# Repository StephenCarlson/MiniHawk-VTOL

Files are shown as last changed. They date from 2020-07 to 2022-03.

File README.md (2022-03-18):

<!-- MiniHawk-VTOL README.md - Enable Word wrap in your Text Viewer/Editor -->
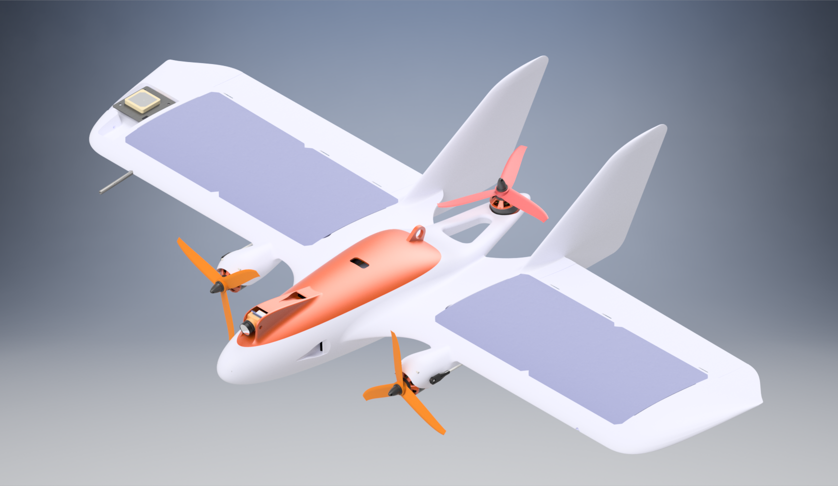
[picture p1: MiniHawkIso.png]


# MiniHawk-VTOL 
The MiniHawk VTOL is a 3D-Printed Tricopter/Fixed-wing hybrid aircraft, capable of Vertical Take-off and Landing. As with its predecessor, the [OrangeHawk VTOL](https://diydrones.com/profiles/blogs/the-orange-hawk-tricopter-flying-wing-vtol-uav), the MiniHawk is intended for R/C, FPV and UAV experimentation.  Mechanical artwork, build instructions, and configuration settings are provided in this repository.  

> **⚠️READ-ME - PROJECT STABILITY AND NEW VERSION⚠️ - 18 MARCH 2022: More than likely, you have stumbled on this project from a link on a YouTube video, such as [How NOT to Flight Test a VTOL UAV](https://www.youtube.com/watch?v=FYqH4kHllrU) or one of the other videos out there. If you want to try making this project, go for it! As of this writing, all the STL files on this repo, the _Version 2.0 - Hotfix and 2.1 Preview_ zip file at the left of this text, and the most recent upload to the Hackaday.io page are "safe". Previously, the were some design flaws (the old tilt nacelle design), but these issues only exist for Version 2.0 STLs from prior to the 23 February Hotfix. Again, everything present on the _master_ branch here should be safe to build and will not be altered for most of 2022.**
> 
> **Now, with that said, there is a new version coming out soon™, Version 2.1. However, at this point, this next version will not change any of the current STLs, so, again, you are totally safe to use the STLs, everything is working and flying great, and no changes to the aircraft design will be released until late this year or early next year. What the release of V2.1 will do is add some new bonus STLs/features, and otherwise it is just polishing presentation or rewriting documentation. I've been stuck in the prerelease of Version 2.1 for a few months, so some parts of this README are being rewritten, such as the build instructions and adding the Parts Tree Diagram and such. Here are my recommendations for building the project at this moment in time:**
> 
> - Refer to the [Development-Branch Build Instructions](https://github.com/StephenCarlson/MiniHawk-VTOL/tree/development#build-sequence-) for the updated build instructions.
> - Browse the [Development-Branch Documentation Folder](https://github.com/StephenCarlson/MiniHawk-VTOL/tree/development/doc-Documentation) for all the new build instruction images; many of these are not yet added or used in the updated build instructions.
> - Watch [MiniHawk-VTOL Assembly in 100 Seconds](https://www.youtube.com/watch?v=nICNlJhoEvw) to see the animated build steps.
> - Cross-reference with the [Older Build Instructions Below](https://github.com/StephenCarlson/MiniHawk-VTOL#build-sequence-). You will see images and steps for the older Version 1.0 release, so ignore features that do not exist or have been redesigned in the intervening 1.5 years.
> 
> **Sorry for the mess, I hope this helps. I enjoy promoting and polishing this project where I have time. Let me know if you have any questions, and have fun building! -Steve**

**Milestones**
| Date | Event |
|---|---|
| 15 Oct 2020  | Initial Release (v1.0) |
| 2 Oct 2021 | Version 2 (v2.0, MH7_ prefix) |
| prerelease | Version 2.1 |
| Q1 2023 | Version 2.2 |

Project Page at Hackaday: [HACKADAY.IO Page](https://hackaday.io/project/175286-minihawk-vtol)  

MiniHawk Design Details and Features discussed here: [RCGroups VTOLs Forum Thread](https://www.rcgroups.com/forums/showthread.php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)  

Featured MiniHawk-VTOL Builds by community members: [RCGroups 3D-Printed Forum Thread](https://www.rcgroups.com/forums/showthread.php?3750791-KatanaGuy-s-MiniHawk-VTOL)

Accompanying Build Video Series: [YouTube Playlist](https://www.youtube.com/playlist?list=PLEMjH2uELUcYI_DS1zthgjE4Su79LeA_G)  

Betaflight VTOL Firmware Build: [vtol-motor-mix](https://github.com/StephenCarlson/betaflight/tree/vtol-motor-mix)  

# Table of Contents
1. [Introduction](#head-brief)  
  1.1 [Description](#head-description)  
  1.2 [How To Use This Repo](#head-usage)  
  1.3 [Remarks / FAQs](#head-faqs)  
  1.4 [Metrics](#head-metrics)  
2. [Build Information](#build-brief)  
  2.1 [Recommended Tools](#build-tools)  
  2.2 [Components and Electronics](#build-components)  
  2.3 [Airframe Parts Listing](#build-airframeparts)  
3. [Build Steps](#buildseq-brief)  
  3.1 [Part 1 - Airframe Structures](#buildseq-part1)  
  3.2 [Part 2 - Linkages and Servos](#buildseq-part2)  
  3.3 [Part 3 - Electronics and Finishing](#buildseq-part3)  
4. [Flight Testing](#flight-brief)  
5. [3D Printing Guidelines](#3dprinting-brief)  
6. [ArduPlane](#arduplane-brief)  
  6.1 [R/C Controls Configuration](#arduplane-controlsconfig)  
  6.2 [Flight Controller Connections](#arduplane-connections)  
  6.3 [Parameters](#arduplane-parameters)  
  6.4 [Remarks](#arduplane-remarks)  
8. [License](#license-brief)  

## Description 
The MiniHawk is a 3D-Printed VTOL aircraft. It was designed with printability in mind, and is intended to provide the community with a common and accessible VTOL testbed for experimentation and tinkering. The vehicle uses three (3) brushless DC motors for propulsion, with the forward pair tilting for forward flight and yaw control, and the rear motor fixed for hover only. Four (4) servos are used to tilt the forward motors and to control the elevon control surfaces of the wing. The airframe is a "plank"-style wing with a center body containing avionics and battery, and internal conduits routing to the nacelles and servos. Twin vertical stabilizer fins provide mild directional stability.  

## How To Use This Repo 
This project is hosted on GitHub, which is traditionally a software repository site, but the format works well for a hardware project such as the MiniHawk-VTOL, where a few of the features come in handy:
- The history for each part file is accessible; if you need an old version, it is available even off-line if you've "cloned" the repo. (Beware, cloning the repo means hundreds of MB download.)
- [Versions and Releases](https://github.com/StephenCarlson/MiniHawk-VTOL/releases) are published just like a software project, and this includes setting milestones and planning future releases, keeping the community informed about what is next. Releases are the condensed set of essential files, placed in a zip archive, which represent a snapshot of the project at a moment when the artwork is stable and worth broad public distribution.
- The [Issues](https://github.com/StephenCarlson/MiniHawk-VTOL/issues) tab allow for the community to participate in the evolution of the design by providing feedback or contributions toward improving the design.
- The [Discussions](https://github.com/StephenCarlson/MiniHawk-VTOL/discussions) tab is another location for communication on the project.

While I have described the hosting environment, it isn't necessary for you to make a GitHub account or participate in the project; and more than likely, you are just interested in downloading the STLs and making the plane. Here is what you need to do:
- Click on the [Latest Release](https://github.com/StephenCarlson/MiniHawk-VTOL/releases/latest) in the Top-Right section of this webpage. This will take you to the most recent version of the design that was stable. 
- Read the description to understand what is new or notable for the release, and then look under the Assets section and find the .zip file named `MiniHawk-VTOL-x.x.x.zip`, where the 'x''s are the release version numbers. Skip the `Source Code` downloads as these are auto-generated by GitHub and represent the entire contents of the project, which you probably are not interested in unless you really want all of it.
- Unzip the archive and examine the files. A snapshot of this README you are reading is contained in the README.md file, and it should be able to be opened by any text editor.
- Follow the [Build Steps](#buildseq-brief) below. It should be possible to print this page or save as a PDF. If you are code-savvy, this is all written in Markdown and should render in whatever text editor or Markdown renderer you prefer.

## Remarks / FAQs 
- As this is a totally 3D-printed airframe, the fully-finished vehicle is moderately heavy, which is a handicap, especially in the hovering mode of flight. As such, be gentle and cautious in adding any additional weight. For the recommended print settings with a 0.4mm nozzle on standard PLA, the airframe alone weights a bit over 460g, and the all-up-weight of the finished vehicle is between 1000g to 1200g.  
- The parts used in this project are commonly available in the drone racing and R/C plane market(s). Standard motors such as 2207, 2306 or similar can be used. The nacelle design dictates a maximum motor bell diameter of 29mm, but this is relaxed compared to previous versions of the design that had more stringent requirements. The Ball-Stud Linkage is perhaps the most specific part used, with Dubro #181, Dubro #190, or even Dubro #367 as acceptable options. 
- The aerodynamics and stability of the vehicle are still under analysis and subject to revision. The CFD poses/cases used for aerodynamics analysis are included for independent study.  
- As of Version 2 of this design, project files are prefixed with "MH7", as this is the 7th internal revision of the design of the MiniHawk VTOL. There may be some old "MH5" parts are retained in the repo; these are from the old version(s). Also, the "MH#" prefix is incidental and not to be confused with the MH airfoil series, of which the MH45 is used for this vehicle. Generally, "MiniHawk-VTOL" is the correct name for this design and any revisions to be released.
- This vehicle was designed in Autodesk Inventor Professional 2019. While compiled STLs are provided as open-access, the Solid Model and Assembly Source files for this vehicle are withheld at the time of this writing; contact me for inquires on obtaining a copy or further development. One minor accommodation: STEP/STP versions of some parts such as the Hatch/Lid are included for community derivations.
- There are some variants to each part, such as versions of the nose with and without NACA vents. The Winglet is available as "normal" or with an excavation for a GPS or other devices. The Hatch/Lid has a FPV Variant, which supports the Foxeer -Nano camera formfactor (15mm width) and has a 30.5mm grid for a video transmitter, such as the AKK Infinite DVR. All the part options and variations are detailed below in the [Parts Tree Diagram](#build-airframeparts).

## Metrics 
| Description | Value |
|---|---|
| Wing Span | 800mm |
| Wing Area | 15.6dm^2 |
| Aspect Ratio | 4.1 |
| Airfoil (Root and Tip) | [MH45][1] |
| Length | 520mm |
| Rotor Spacing | 315mm Circle |
| Lipoly Battery | 4s, 1300-1500mAh (~160g)  |
| Motors (front) | 2207 or 2306 2300-2600kV  |
| Motor (rear) | 2207 or 2306 ~2000kV |
| Servos | HS-65HB/MG or eqv. |
| Flight Controller (size) | 30.50mm to 16.0mm Grid |
| Propellers (front) | 5050 to ~5249 |
| Propeller (rear) | 6030 to ~5249 |
| All-up Weight | 1000g to ~1200g w/ PLA |

[1]: <https://www.mh-aerotools.de/airfoils/mh45koo.htm> "MH45 Airfoil by Martin Hepperle"

# MiniHawk Build Parts List and Tools 
## Recommended Tools and Equipment 
 - FDM/FFF 3D Printer with build volume greater than 23.1x210.7x150mm (A build height of 330mm or greater will allow for printing the nose and wings as single parts rather than split.)
 - Soldering Station and associated tools and materials for electronics crafting
 - Handcrafting Tools: Pliers, Side-Cut Diagonal Cutters, Sandpaper, Hobby Knife/Scalpel, Hand Drill, etc
 - Adhesives and Consumables: Cyanoacrylate Glue, Hot-Melt Adhesive Gun, Tape

## Components and Electronics 
| Qty | Item Description | Notes |
|-----|---|---|
| 1 | Flight Controller (3 Motor, 4 Servo Outputs) | mRo PixRacer Pro, Matek F405-WING or F765-WING |
| - | Pitot Probe, GPS, Telem. Radios, FPV Cam+VTx, etc | Additional Essential Avionics |
| 1 | UBEC for servo power if not built into Flight Ctrlr. | Castle Creations 10 Amp Adjustable BEC |
| 1 | R/C Receiver, 8+ Channel, SBUS or PPM Output | |
| 3 | ESC (4s, 40A or better) | EMAX Formula Series 32Bit 45A ESC |
| 2 | 2207 or 2306 ~2500KV BLDC Motor (Out.Dia. < 29mm) | T-Motor VELOX V2 2207 2550Kv (Note 1) |
| 1 | 2207 or 2306 ~2000KV BLDC Motor | T-Motor VELOX V2 2306 1950Kv (Note 2) |
| 1 | 4s1300 Lipoly (60C or better) | RDQ 14.8V 4S 1300mAh 100C |
| 1 | XT60 Pigtail or equiv. | |
| 2 | HS-65HB Servo (or equiv.) | Elevon Servos, see (Note 3). |
| 2 | HS-5065MG Servo (or equiv.) | Motor Tilt Servos, see (Note 4). |
| 1 | Carbon Fiber Spar, Length<640mm, Out.Dia.<=6.5mm | Used to strengthen the wings. Round or Square |
| 6 | (opt) Du-Bro SKU#118 Small Nylon Hinge | Elevon Reinforcement, see (Note 5). |
| - | M2 or M3 Mounting Hardware (Nuts, Bolts, Standoffs)  | For mounting Flight Controller, trays. |
| 4 | 6-Inch Servo Extension Cable | (Note 6) |
| 1 | Male-to-Male Servo Extension Cable | Flight Controller to Receiver PPM/SBUS connection. |
| 4 | 2-56 Link Clevis (Note 7) | Four (4) servo arm connections. |
| 2 | 2-56 Threaded Linkage Rod, Length>=52mm | Elevon pushrods, L-bend at 45mm from threaded tip. |
| 2 | (opt) Du-Bro SKU#855 E/Z Links 0.72 (2-56) Clip | For securing L-Bends, can replace with Z-bend. |
| 2 | 1/16-inch 2-56 Ball Link and Coupler Pair | Dubro #181 or Dubro #190, see (Note 8). |
| 2 | 2-56 Fully-Threaded Rod, Length=70mm | End1=(Link 2-56 Clevis), End2=(2-56 Ball Coupler)  |
| 2 | 2-56 Smooth Rod, Length=40mm | (Note 9) |
| 4 | (opt) 3mm Bolt or Shaft, Length=44mm | If you want to use ball bearings to the tilt arms. |
| 4 | (opt) 3x6x2.5mm Ball Bearing | Commonly known as MR63ZZ, for tilt arm supports. |
| 2 | (opt) WS2812 5050 SMD (or equiv. Addressable LED) | Soldered with magnet wire, mounted in wingtips. |
| - | M4 or M5 Prop Nuts | Replace default prop nuts if needed |
| 1 | 50xx Propeller, Clockwise Rotation | Left/Port-side Propeller, 5-inch |
| 1 | 50xx Propeller, Counterclockwise Rotation | Right/Starboard-side Propeller, 5-inch |
| 1 | 50xx or 60xx Propeller, Counterclockwise Rotation | Tail Propeller, Dalprop Foldable F6 6048 Tri-blade |
| 1 | Velcro Battery Strap | |
| 1 | (opt) Battery Voltage Monitor / Alarm Buzzer | For Flight Controller if not included. |

> Note 1: Front motors should be no larger than OutsideDiameter=29mm, able to produce between 500g to 800g static thrust (@full-throttle), and pitch speed of ~20m/s (@half-throttle) with 5-inch prop.  
> Note 2: Tail motor may be up to OutsideDiameter=30mm or more, able to produce between 700g to 1000g static thrust (@full-throttle) with up to a 6-inch prop.  
> Note 3: Servo bays are designed for up to 26mm wide servos, 17.5mm from bottom of mounting tabs to bottom of servo, 32mm from top of output shaft to bottom of servo, 12mm thick. Should fit most "Sub-Micro" Servos.  
> Note 4: Same pocket dimensions as above, but these are going to be fantastically abused and must be fairly tough. Or just count on stripping your non-metal-gear servos a lot.  
> Note 5: Can be omitted, but 3D-printed living-hinge on elevons will eventually fail, mend appropriately. Dubro #118 is 6 per package, Dubro #119 for 15/pkg.  
> Note 6: Alternatively, cut the servo cables and solder in-line extensions for the cables to reach to the flight controller, plus some slack.  
> Note 7: The clevises and rods can be purchased as a set, such as Du-Bro #185, which is a set of 5 rods with clevises already attached.  
> Note 8: The Ball Link thread size should be 1/16-inch / 62.5mil / 1.59mm. A more popular variant of this type of part has a 2-56 (86mil) thread size ball, which a bit large but should be adaptable to the nacelle motor tilt mount part. If you can only order metric hardware, 2mm thread size should be fine. Note that this is the ball-link-stud thread size; the ball-link-stud attaches to the ball-link-socket/coupler that captures a threaded rod, which then links to the servo arm. This linkage rod which goes between the servo arm and the ball-link-socket/coupler can be any size, but is assumed to be 2-56 here.
> Note 9: Diameter=[1.83mm to 1.87mm], formed from spare pieces of 2-56 Servo Pushrod. Use non-threaded smooth rod, roughen/knurl only one end slightly for press-fitting to nacelle.  

## Airframe Parts 

```
MiniHawk-VTOL Version 2.1 Aircraft
|-- Fuselage/Body  
|   |-- Empennage/Tail
|   |   |-- Print Option 1: As a Single Part - No Split, but layers are not aligned for max. strength
|   |   |   |-- MH7_Empennage-Full.stl
|   |   |
|   |   |-- Print Option 2: Split into Two Parts with print layers aligned for strength
|   |       |-- Print Option 2a: Explicit Print Supports
|   |       |   |-- MH7_Empennage-PrintSupports.stl
|   |       |
|   |       |-- Print Option 2b: No Explicit Print Supports, plain part
|   |           |-- MH7_Empennage.stl
|   |
|   |-- Nose
|   |   |-- Print Option 1: Full Nose - No Split
|   |   |   |-- MH7_Nose.stl
|   |   |
|   |   |-- Print Option 2: Nose in Two Pieces
|   |       |-- MH7_Nose_A.stl
|   |       |-- MH7_Nose_B.stl
|   |
|   |-- Avionics (Flight Controller) Tray
|   |   |-- Part Variant: Solid Tray, No Vibration Dampening
|   |   |   |-- MH7_AvionicsTray.stl
|   |   |
|   |   |-- Part Variant: Leaf-Spring Compliant-Mechanism Vibration-Dampening Version
|   |       |-- MH7_AvionicsTray2.stl
|   |
|   |-- Battery Tray
|       |-- MH7_BatteryTray.stl
|
|-- Hatch/Lid
|   |-- Part Variant: FPV 16mm-sized Camera and VTx Support
|   |   |-- Print Option 1: Long-axis Symmetric Half (TODO: Needs to be restored to -Full)
|   |   |   |-- MH7_Hatch-FPV-16mm.stl
|   |   |
|   |   |-- Print Option 2: Split into Two Parts for nicer print
|   |       |-- MH7_Hatch-FPV-16mm_a.stl
|   |       |-- MH7_Hatch-FPV-16mm_b.stl
|   |
|   |-- Part Variant: Vented with NACA Duct
|   |   |-- Print Option 1: Entire thing, split it yourself
|   |   |   |-- MH7_Hatch-Vented.stl
|   |   |
|   |   |-- Print Option 2: Split into Two Parts for nicer print
|   |       |-- MH7_Hatch-Vented_a.stl
|   |       |-- MH7_Hatch-Vented_b.stl
|   |
|   |-- Locking Latch Mechanism
|       |-- MH7_Hatch_LockingLatch.stl
|       |-- 1.85mm Steel Pin, Length=30mm
|
|-- Left Wing  
|   |-- Part Variant: Plain Wing
|   |   |-- Print Option 1: Entire wing
|   |   |   |-- MH7_WingLeft.stl
|   |   |
|   |   |-- Print Option 2: Split into Two Parts for smaller printers
|   |       |-- MH7_WingLeft_A.stl
|   |       |-- MH7_WingLeft_B.stl
|   |
|   |-- Part Variant: Solar Wing
|   |   |-- Print Option 1: Entire wing
|   |   |   |-- MH7_WingLeft-Solar.stl
|   |   |
|   |   |-- Print Option 2: Split into Two Parts for smaller printers
|   |       |-- MH7_WingLeft_A.stl
|   |       |-- MH7_WingLeft_B.stl
|   |
|   |-- Elevon Control Horn
|       |-- MH7_ControlHorn.stl
|
|-- Left Fin  
|   |-- MH7_FinLeft_Lower.stl  
|   |-- MH7_FinLeft_Upper.stl  
|
|-- Left Nacelle
|   |-- Part Variant: Ball Bearing Version
|   |   |-- MH7_Nacelle_A-Bearing.stl
|   |   |-- MH7_Nacelle_B-Bearing.stl
|   |
|   |-- Part Variant: Non-Ball Bearing Version
|   |   |-- MH7_Nacelle_A-NoBearing.stl
|   |   |-- MH7_Nacelle_B-NoBearing.stl
|   |
|   |-- Motor Tilt-Mount
|       |-- Part Variant: Ball Bearing Version
|       |   |-- MH7_TiltMount_A-Bearing.stl
|       |   |-- 3mm Shaft or Threaded Bolt, Length=44mm
|       |
|       |-- Part Variant: Non-Ball Bearing Version
|       |   |-- MH7_TiltMount_A-NoBearing.stl
|       |   |-- 1.85mm Steel Pin, Length=40mm
|       |
|       |-- MH7_TiltMount_B.stl
|       |-- BLDC Motor
|    
|-- Left Winglet
|   |-- Part Variant: Plain Winglet
|   |   |-- MH7_WingletLeft.stl
|   |
|   |-- Part Variant: GPS Pocket
|       |-- MH7_WingletLeft-GPS.stl
|
|-- Right {Wing, Fin, Nacelle, Motor Tilt-Mount, Winglet} 
|   |-- For each of the symmetric parts, to create the right-side version, simply mirror the part in your slicer software. 
        Be _very careful_ please! Be sure you understand how all the parts go together, particularly the Nacelle pieces: 
        The nacelle _A piece is always near the aircraft center body, with the _B piece on the outboard side, aligned with 
        the servos and away from the center body. You should print four unique Nacelle pieces, with no two alike: 
        Two non-mirrored pieces of _A and _B, and two mirrored pieces of _A and _B.

Supporting Devices and Parts
|-- Weight & Balance Jackpoint Stand
|   |-- Nacelle-Support Beam
|   |   |-- MH7_WeightBalanceStand_Beam.stl
|   |   |-- MH7_WeightBalanceStand_Support.stl
|   |   |-- Two 1.85mm Steel Pins, Length=50mm each
|   |
|   |-- Empennage-Support Jack
|       |-- MH7_WeightBalanceStand_Foot.stl
|       |-- MH7_WeightBalanceStand_Support.stl (After gluing, bend the legs with hot water to form a triangle stance)
|       |-- 1.85mm Steel Pin, Length=50mm
|
|-- STEP/STP Version of the Hatch/Lid for Community Mods
    |-- MH7_Hatch_RELEASED.stp
```

# Build Sequence 
The following instructions assume that a full set of airframe parts have been printed, as enumerated above. Refer to the [3D Printing Guidelines Section](#3dprinting-brief) for details on the typical slicer settings for each part. Also, 3MF production files are available in the [3mf-Implementations](/3mf-Implementations) repo folder, but whether the print settings properly transfer to your particular printer is a bit of a gamble.

[Figure-1]: </doc-Documentation/Figure-1.png> "Figure 1 - Hinge Pin Clearance" 
[Figure-2]: </doc-Documentation/Figure-2.png> "Figure 2 - Elevon Movement Cuts"
[Figure-3]: </doc-Documentation/Figure-3.png> "Figure 3 - Hatch/Lid Bonding"
[Figure-4]: </doc-Documentation/Figure-4.png> "Figure 4 - Empennage Halves Bonding"
[Figure-5]: </doc-Documentation/Figure-5.png> "Figure 5 - Elevon Control Horn Install"
[Figure-6]: </doc-Documentation/Figure-6.png> "Figure 6 - Empennage/Tail Attachment"
[Figure-7]: </doc-Documentation/Figure-7.png> "Figure 7 - Nacelle Halves Bonding"
[Figure-8]: </doc-Documentation/Figure-8.png> "Figure 8 - Wing Attachment"
[Figure-9]: </doc-Documentation/Figure-9.png> "Figure 9 - Nacelle Pocket Finishing"
[Figure-10]: </doc-Documentation/Figure-10.png> "Figure 10 - Shaft and Bolt Hole Reaming"
[Figure-11]: </doc-Documentation/Figure-11.png> "Figure 11 - Nacelle Attachment"
[Figure-12]: </doc-Documentation/Figure-12.png> "Figure 12 - Vertical Stabilizer Attachment"
[Figure-13]: </doc-Documentation/Figure-13.png> "Figure 13 - Strake Attachment"
[Figure-14]: </doc-Documentation/Figure-14.png> "Figure 14 - Linkages and Movements"
[Figure-15]: </doc-Documentation/Figure-15.png> "Figure 15 - Propeller Rotation Directions"
[Figure-16]: </doc-Documentation/Figure-16.png> "Figure 16 - Center of Mass"

## Part 1 - Airframe Structures and Motor Mount/Tilt Attachment 
1. Clean all 3D-Printed parts, remove all brim/support material. Remove any burrs or blemishes. For each wing, carefully carve away any stringing or over-extrusion in the hinge reinforcement wells such that the hinge pin will fit. [Figure-1] The pitot-probe shaft and other small features may also have stringing that should be removed.  

2. Carefully cut the elevons free if needed (**WARNING!** Only cut slots on either end to allow for surface deflection, DO NOT cut the entire elevon out). [Figure-2] Gently exercise each surface up and down until the living hinge is established. The best way to start is to bend the elevons downward (as if pitching nose down) with a solid planar object to distribute the pressure on the control surface evenly. Only go as far as you feel comfortable, and then reverse direction. Continue to exercise the hinge gently until it is moving +/- 30 degrees. If you printed with PLA or another work-hardening material, don't continue cycling the hinge until the reenforcement tape or tabs are installed; only then should the hinge be further broken-in until it has smooth movement.  

<!-- Hey, if you are reading this, GitHub makes it really hard to inject pictures in a table with nice rows and spacing. -->
<!-- The HTML below renders the figures nicely in GitHub as of December 2021, may not work in other Markdown Processors. -->
<table style="width:100%">
  <tr>
    <td><figure>
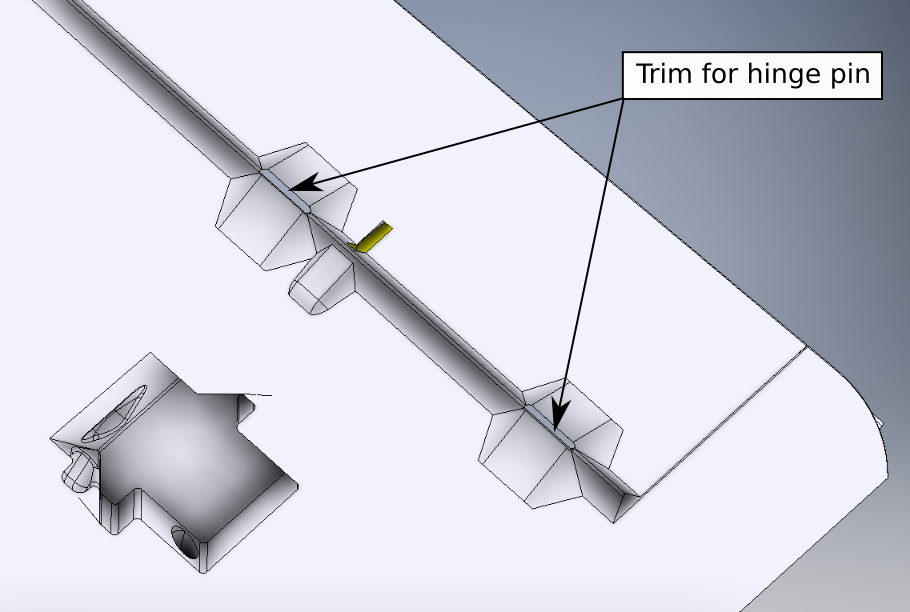
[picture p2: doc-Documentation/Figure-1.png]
      <br>
      <figcaption>Figure 1. Hinge Pin Clearance</figcaption></figure></td>
    <td><figure>
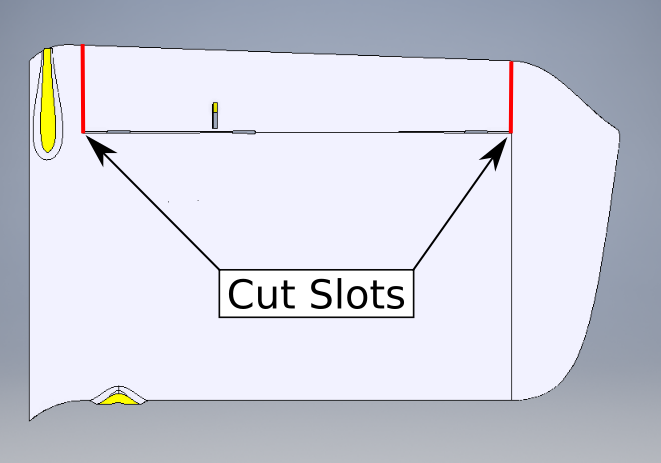
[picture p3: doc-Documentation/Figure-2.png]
      <br>
      <figcaption>Figure 2. Elevon Movement Cuts</figcaption></figure></td>
  </tr>
</table> 

3. Bond the Canopy/Hatch-Lid pieces together using Thin/Medium Cyanoacrylate and set aside to cure. [Figure-3]  

4. Bond the Empennage Halves together using Cyanoacrylate. (Skip this step if you printed the -Full one-piece version.) Set aside to cure. [Figure-4]  

<table style="width:100%">
  <tr>
    <td><figure>
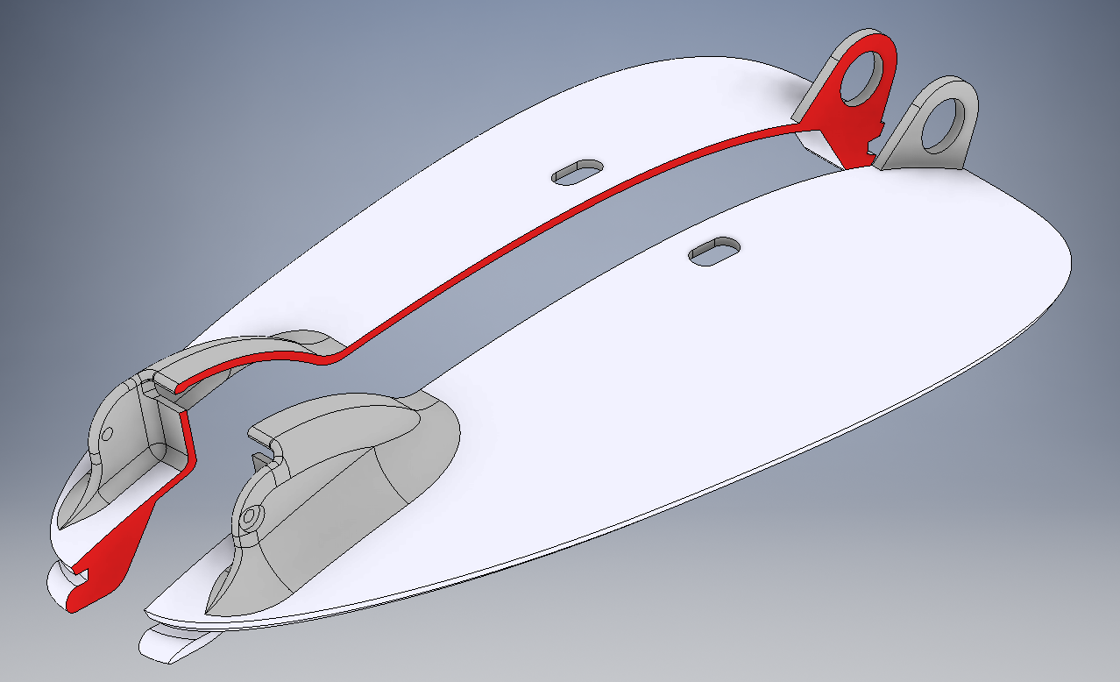
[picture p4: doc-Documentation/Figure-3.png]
      <br>
      <figcaption>Figure 3. Hatch/Lid Bonding</figcaption></figure></td>
    <td><figure>
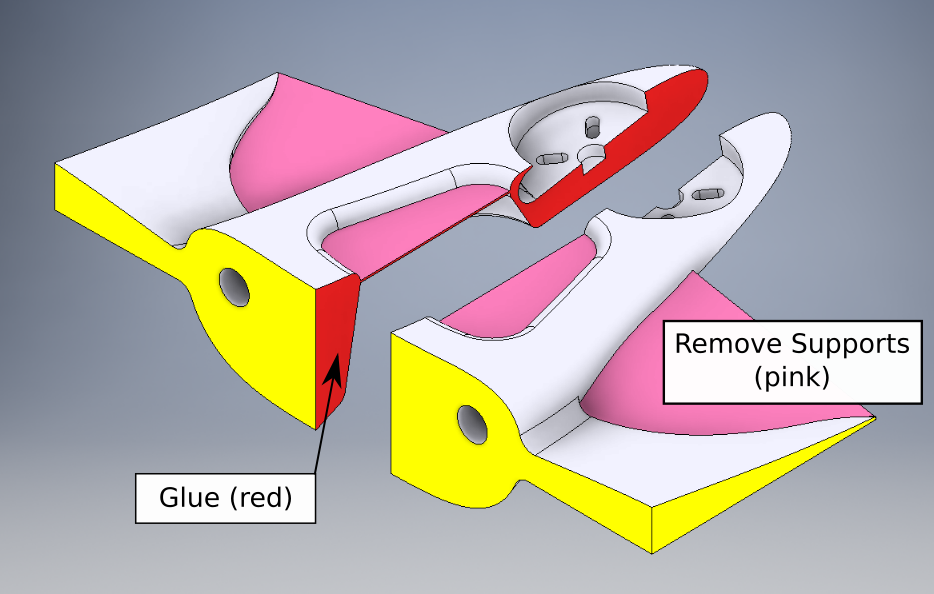
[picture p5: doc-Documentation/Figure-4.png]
      <br>
      <figcaption>Figure 4. Empennage Halves Bonding</figcaption></figure></td>
  </tr>
</table> 

5. Press-fit the Control Horn pieces into the elevons to test the fit. The Control Horn is inserted from the top, protruding through the elevon with the hole centered below the hingeline, inline with the elevon servo linkage. The pieces should be fairly flush on the Elevon Top Surface, with approximately 0.5mm extending above the surface. The fit should be tight, but do not force the control horn too hard or you may split print layers and cause damage. If it is too tight, carefully carve away any burrs or over-extrusion from the slot in the elevon, or sand the control horn to be thinner. Bond the Control Horn pieces (2) into each Elevon (Left Wing and Right Wing) using Cyanoacrylate. [Figure-5]  

6. Glue the Du-Bro Nylon Mini-Hinge pieces (3 per wing, Du-Bro SKU#118) into the recesses along each elevon hinge. Hot-Melt-Adhesive or Cyanoacrylate should work. 3M™ Transpore™ Surgical Tape is also a viable hinge reenforcement solution, and this may be applied now or later in the build.  

7. Lightly sand the bonded empennage/tail interface surface until smooth and planar/flush. Test-fit to the Fuselage/Nose to confirm a proper flush joint, and then bond to the Fuselage/Nose using Cyanoacrylate. Set aside to cure. [Figure-6]  

<table style="width:100%">
  <tr>
    <td><figure>
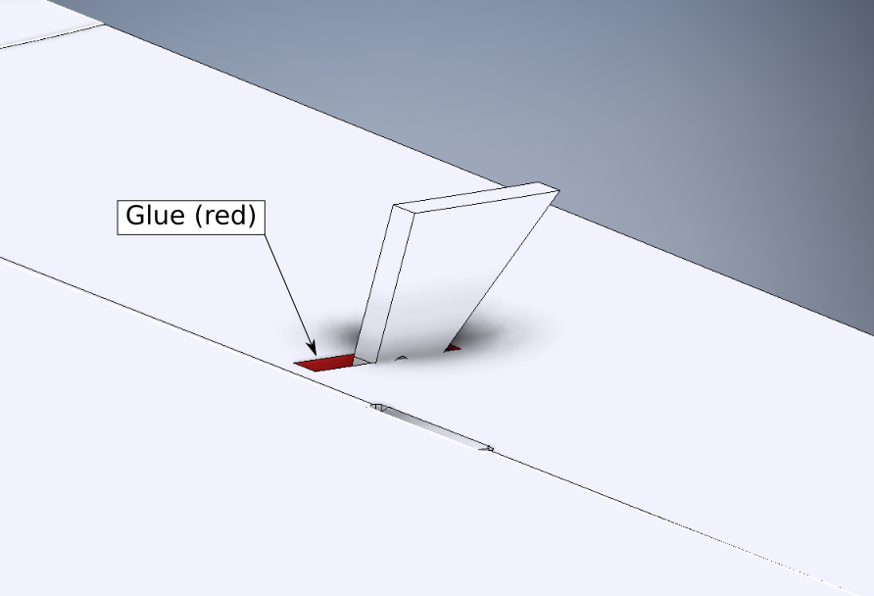
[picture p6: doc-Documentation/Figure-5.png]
      <br>
      <figcaption>Figure 5. Elevon Control Horn Install (Insert from top into slot)</figcaption></figure></td>
    <td><figure>
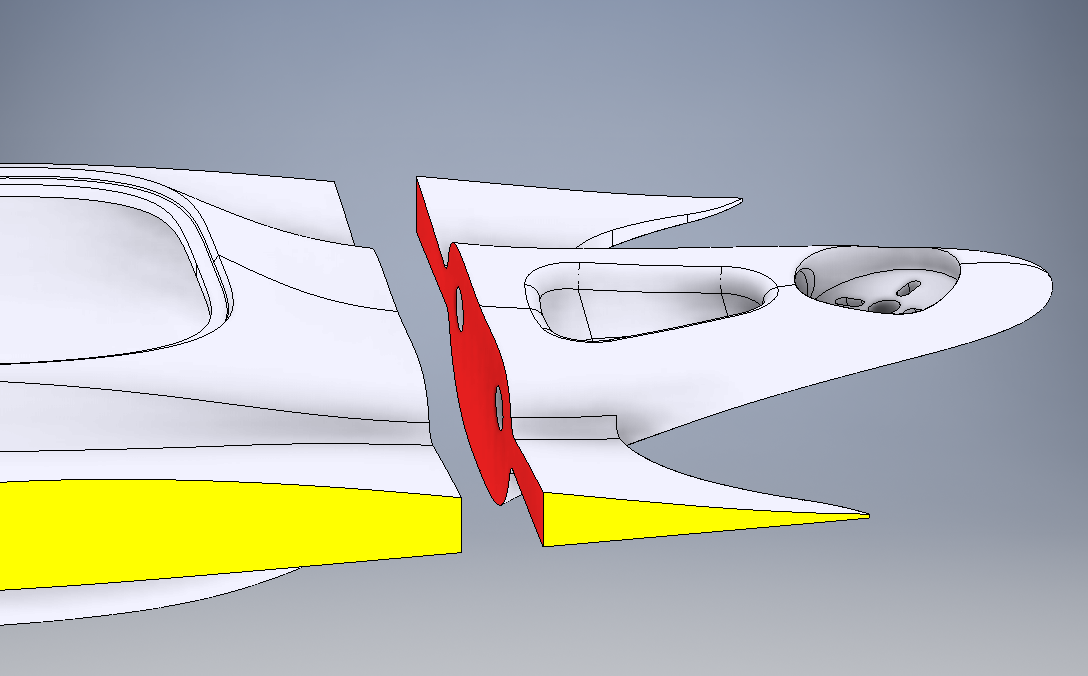
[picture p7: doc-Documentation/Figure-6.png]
      <br>
      <figcaption>Figure 6. Empennage/Tail Attachment</figcaption></figure></td>
  </tr>
</table> 

8. Bond the Nacelle Pair Halves together; **Be careful here!** Each nacelle is composed of an `_A` and `_B` piece. There should be four nacelle pieces total, and each of them is unique: An `_A` and `_B` that are non-mirrored, and a `_A` and `_B` that are mirrored. The `_A` has no cutout for the stud-arm, while the `_B` does. The `_A` pieces are always nearest the center body of the aircraft, and the `_B` pieces are always on the outside aligned with the servos. Glue the pieces together as carefully and precisely as possible, using Cyanoacrylate. Set aside to cure. [Figure-7]  

9. Lightly sand both wing root interface surfaces on the completed fuselage/body until flush and smooth. Test-fit the carbon-fiber spar and verify that it isn't being halted by any blemishes in the spar shaft in either wing. Get creative if there are blemishes; usually some aggressive poking with the spar will clear these without damaging the 3D-printed shaft. If the spar does not completely fill the spar shaft (7mm inside diameter), such as if the carbon spar is a 5mm round tube, then improvise a shim or other filler to make the fit snug, such as wrapping the spar with tape at the ends and near the center where it will exit into the central body cavity. With the spar present to provide alignment, test-fit both wings to each respective surface to confirm a proper flush joint. Center the spar such that it extends into the left and right wings an equal amount. (640mm is the longest spar length supported. A shorter spar is fine provided it is centered.) Remove the wings. At this point, the spar may be bonded to the body, if desired. (The spar can be installed without any adhesive if you plan on reusing it later, such as if the aircraft is totaled but the spar survives.) Bond either the left or right wing to the fuselage (not recommended to attach both at once) using Cyanoacrylate. Set aside to cure. When the first wing is cured, bond the second wing and set aside to cure. [Figure-8]  

<table style="width:100%">
  <tr>
    <td><figure>
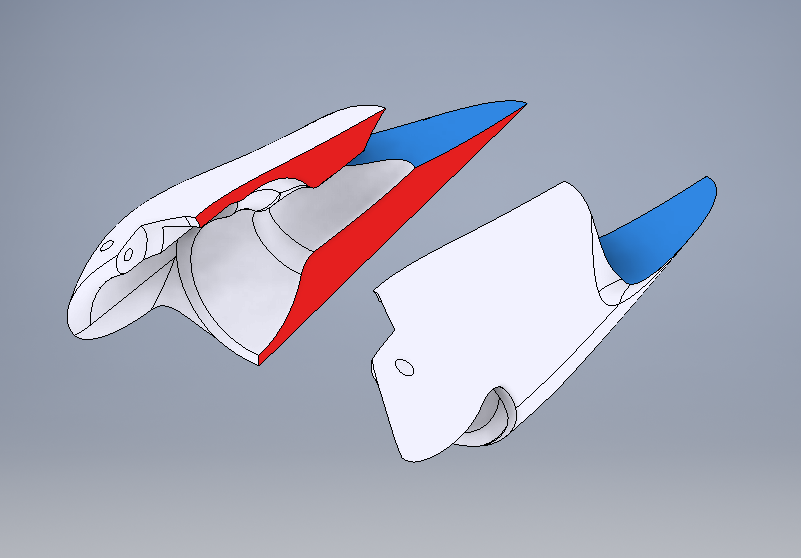
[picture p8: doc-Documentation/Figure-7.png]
      <br>
      <figcaption>Figure 7. Nacelle Halves Bonding</figcaption></figure></td>
    <td><figure>
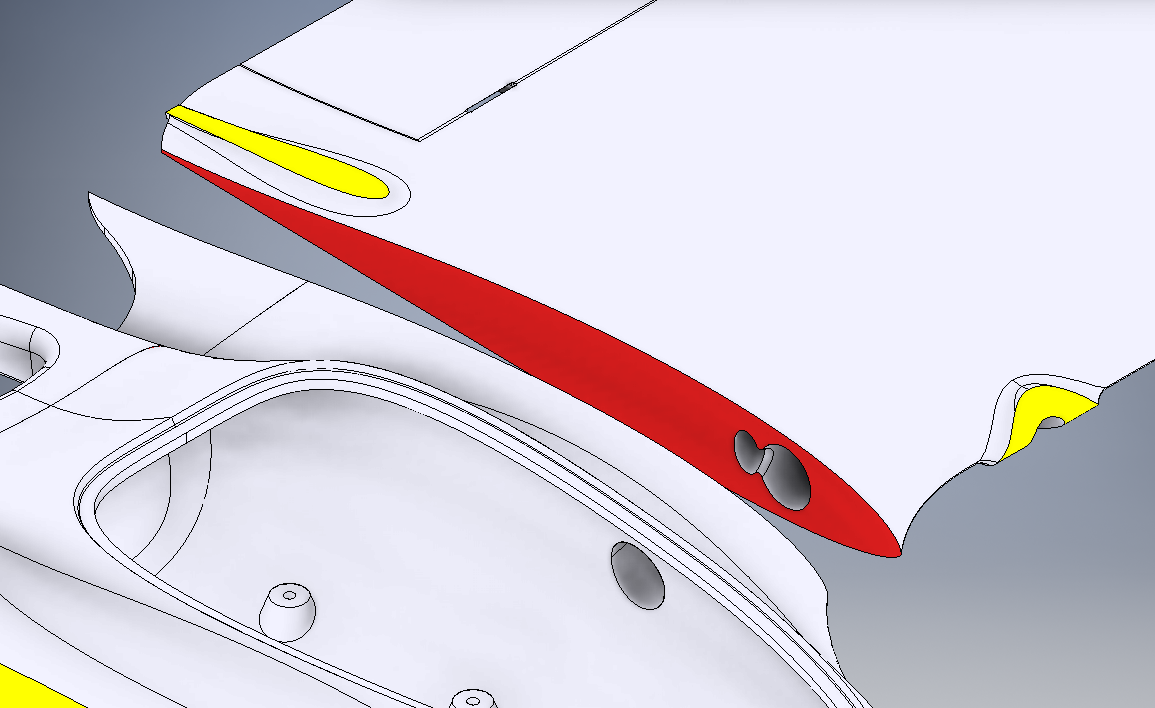
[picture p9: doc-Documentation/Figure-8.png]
      <br>
      <figcaption>Figure 8. Wing Attachment</figcaption></figure></td>
  </tr>
</table> 

10. Test-fit each Motor Mount (Tilt Mount/Pod) with its respective completed nacelle. Sand or trim as needed such that the Motor Mount is able to tilt fully flush forward, and able to tilt up past 90 degrees of rotation. [Figure-9]  

11. (Nacelle Non-Ball-Bearing Version) For each Nacelle with its respective Motor Mount aligned and present, Ream (Drill to size) using a 1.58mm (1/16 Inch, 62.5mil) drill bit. (Should be 85% to 90% of the diameter of hinge rod to be fitted. Hinge Rod diameter is 1.84mm or 72mil for this case.) Keep the Motor Mount and Nacelle together. Adapt a section of hinge rod to be used as a final precision reaming tool by sharpening the tip using a grinder or emery wheel. Use this improvised reaming tool to ream the hole in each nacelle-mount pair to a final diameter of 1.84mm (72mil). [Figure-10]  

<table style="width:100%">
  <tr>
    <td><figure>
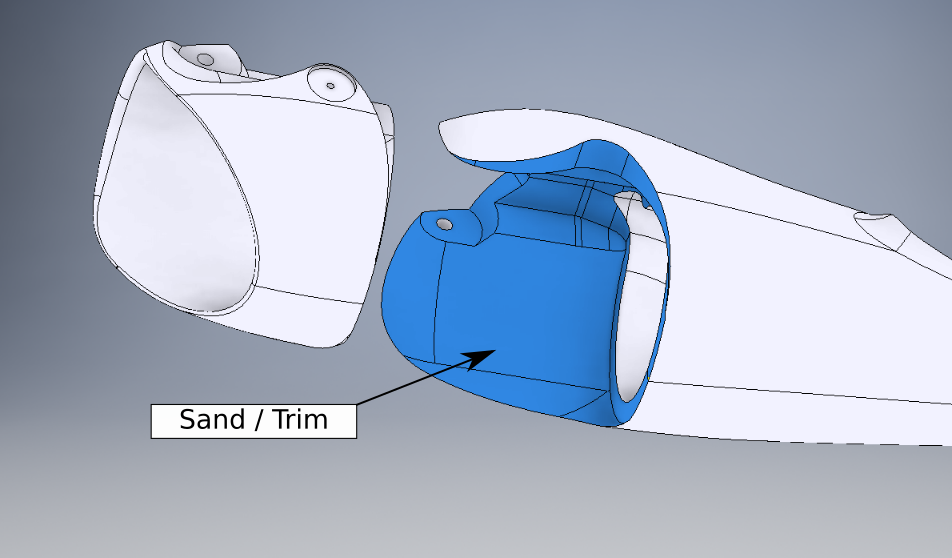
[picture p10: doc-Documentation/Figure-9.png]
      <br>
      <figcaption>Figure 9. Nacelle Pocket Finishing</figcaption></figure></td>
    <td><figure>
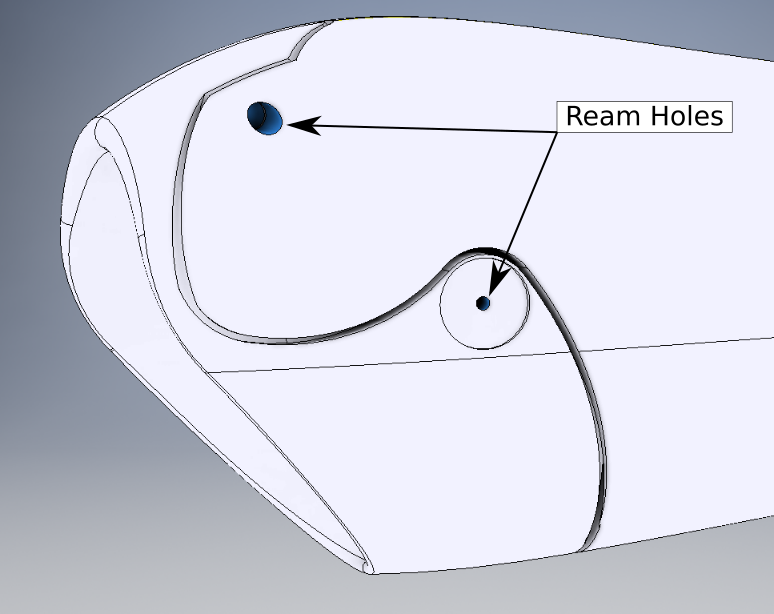
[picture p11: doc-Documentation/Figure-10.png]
      <br>
      <figcaption>Figure 10. Shaft and Bolt Hole Reaming</figcaption></figure></td>
  </tr>
</table> 

12. (Nacelle Ball-Bearing Version) Refer to the above steps for the non-ball-bearing nacelle design, but use a 3.00mm (7/64 Inch, 118mil) drill bit to ream the shaft. The mechanical friction relationship is inverted, with the motor tilt-mount having a strong friction fit with the insert shaft, and the ball bearings in the nacelle forks/arms providing the smooth rotation interface. Press-fit the ball bearings into the pockets, using mild heat only if appropriate. Improvise a shaft retention solution that also captures the bearings and prevents either bearing from dislodging. Avoid improvising a solution that conducts compression on the nacelle "forks", as this would cause binding and friction.  

13. (Nacelle Non-Ball-Bearing Version) Remove each Motor Mount from its respective Nacelle and ream only the Motor Mount hole to the next higher drill bit size, not to exceed 107% of diameter of the the hinge rod. This allows for the outer nacelle arm to have a friction fit retention of the metal shaft, while the inner motor mount is able to rotate smoothly, plastic-on-metal. Too large will allow for excessive play and possible rattling; too small will result in binding. 1.95mm (77mil, 5/64 Inch) is acceptable for hinge rod diameter of 1.84mm.  

14. (Nacelle Non-Ball-Bearing Version) Cut the hinge rod pieces, not to exceed 40mm length. Roughen/knurl one or both ends if desired. Press-fit each hinge rod to each Nacelle through the respective Motor Mount. Verify that each Motor Mount can rotate freely and with minimal play in the hinge.  

15. For each Motor Mount, ream the Motor Mount linkage mount hole to 1.19mm (3/64 Inch, 47mil) if you are using the recommended 1/16 ball-stud. This can potentially be reamed for a larger ball-stud thread size such as 2-56 (1.84mm, 72mil), use careful judgement in this case. The reamed hole should be about 80% of the major diameter of the threaded ball link to be mounted. Mount the threaded ball-link to the linkage mount hole. The Motor Mount can sustain up to 8mm threaded ball-stud bolt depth.  

16. Bond each Nacelle to its respective wing; note that the ball-link should align with the respective servo linkage slot/well. Cyanacrylate works great on PLA, but as this is one of the higher load-bearing structures on the aircraft, epoxy is also a candidate. Verify alignment and tweak/tune the position while the glue cures. [Figure-11]  

17. Bond the Lower and Upper pieces of the vertical fins. [Figure-13] (The lower piece is sometimes called the "Strake".) Bond both vertical fins to their respective wing(s). [Figure-12] Cyanoacrylate should be sufficient.  

<table style="width:100%">
  <tr>
    <td><figure>
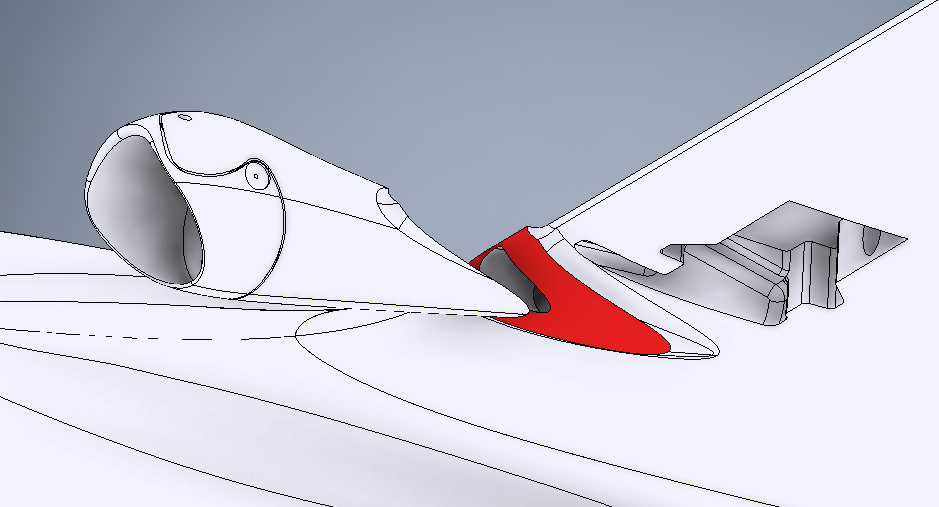
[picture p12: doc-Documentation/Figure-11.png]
      <br>
      <figcaption>Figure 11. Nacelle Attachment</figcaption></figure></td>
    <td><figure>
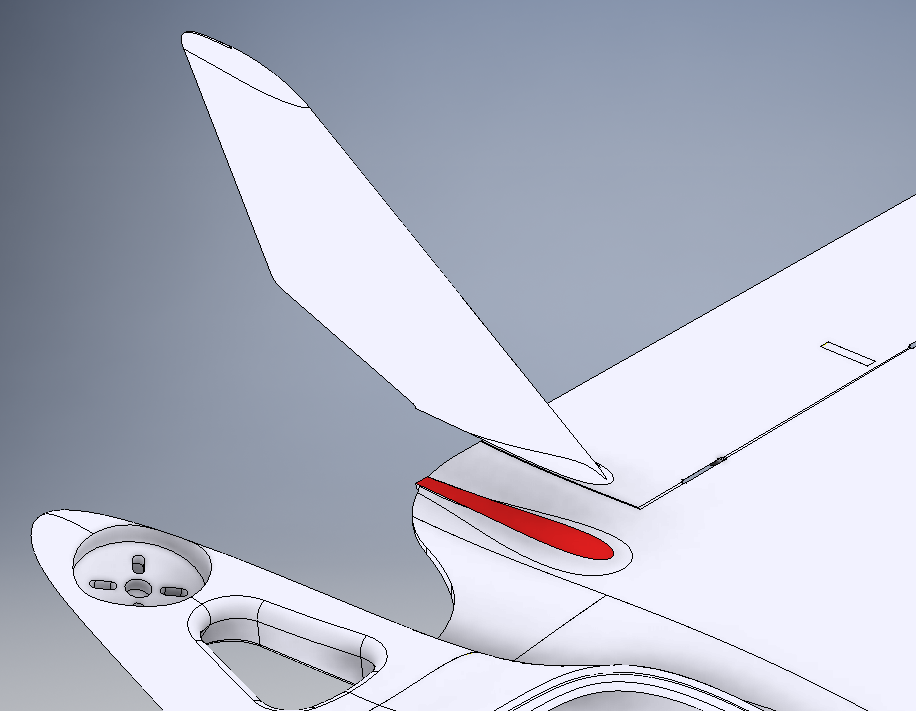
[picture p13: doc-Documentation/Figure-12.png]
      <br>
      <figcaption>Figure 12. Vertical Stabilizer Attachment</figcaption></figure></td>
  </tr>
  <tr>
    <td><figure>
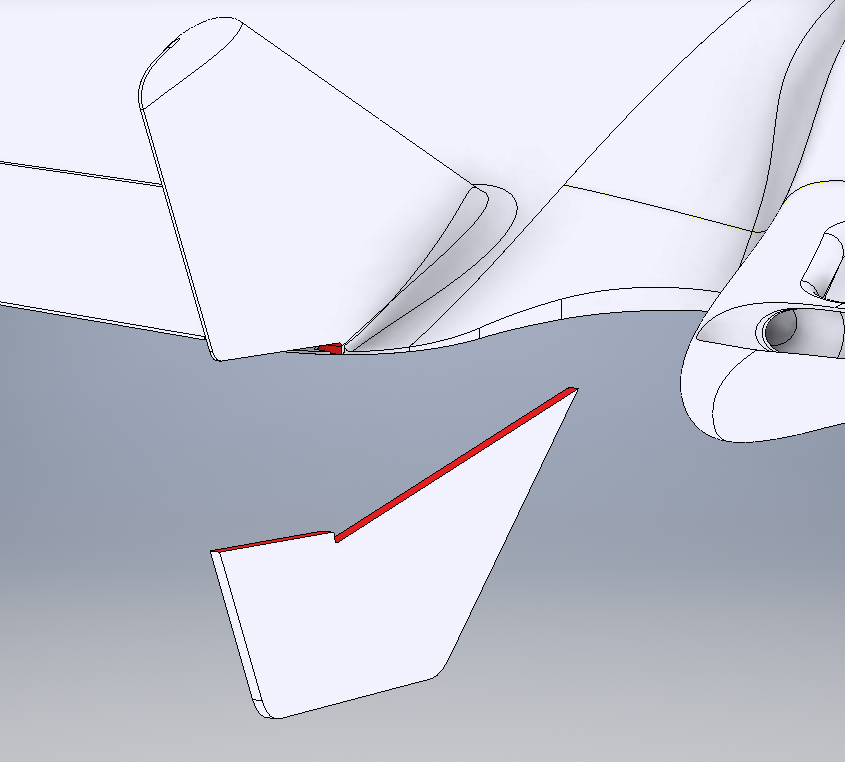
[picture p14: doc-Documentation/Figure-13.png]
      <br>
      <figcaption>Figure 13. Strake Attachment</figcaption></figure></td>
    <td><figure>
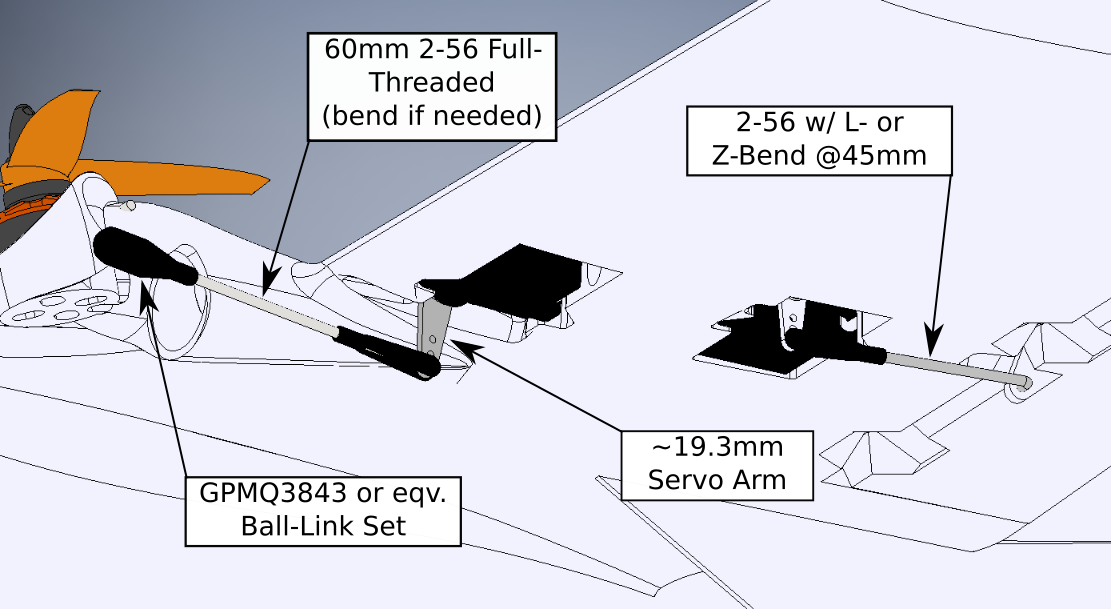
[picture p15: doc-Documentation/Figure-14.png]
      <br>
      <figcaption>Figure 14. Linkages and Movements</figcaption></figure></td>
  </tr>
</table> 

## Part 2 - Linkages and Component Mounting 
1. Mount the front two motors in their respective Motor Mounts. The motor leads may have heatshrink that may interfere or bind the wires; rework this if needed. Mount the motors using the M3 threaded bolt kit that should be included with each motor. Be careful not to have any mounting bolt over-extend into the motor armature/stator. Verify that each motor turns freely and is well secured. Route the wires through the wing and into the main bay, and test the extension-retraction behavior of the wires as the motor mount pitches between forward and hover tilt positions. For each motor, attach the propeller hub hardware kit that should be included with each, such that it can drive a standard 5-Inch propeller.  

2. The Rear motor should mount to the tail using M3 threaded bolts that were included with the motor. Route the motors wires through either wire duct channel to the main bay as desired. (The preferred/traditional channel is the left/port side duct, preserving the right/starboard channel for antennas and LED wiring.) Verify that the motor rotates freely and is well secured. Attach the propeller hub hardware kit that should be included with the motor, such that it can drive a standard 6-Inch propeller. Verify that the propeller clears the vertical stabilizer fins, and trim the tips if necessary, or down-select to a 5-Inch prop.  

3. The Motor Mount Tilt servos should be tested and centered on a standard RC PWM signal, visiting 1000us, 1500us, and 2000us pulse-widths. Attach a servo arm with a 19.3mm (0.76 Inch) hole-to-center spacing. This value is critical, as the linkage behavior of the tilting front motor mounts cannot be easily modified and any length short of this will result in the motor tilt not reaching the needed angle for hover and anti-torque (yaw) control. An arm any longer than this will not fit in the linkage well/slot. With whatever arm fitted as similar to 19.3mm as possible, test fit the servo into the servo well and verify that between 1000us and 2000us pulse widths, the arm comfortably retracts into the well/slot, and fully sweeps about 90 to 95 degrees from that point. Verify the best servo arm spline position, and bolt/secure the arm in place. [Figure-14]  

4. For each of the Elevon servos, repeat the same procedure as above, but with a servo arm approximately 9.5mm hole-to-center (3/8 Inch). This length can be a bit longer or shorter, the effect is increasing or decreasing elevon control throw. For servos that have an odd-number spline tooth count (such as the Hitec HS-65HB's B1 spline with 25 teeth), to get the most well-centered and symmetric solution, center the servo on a 1500us pulse width and alternate attaching a 4-arm output horn between each 90-degree position to find the most orthogonal/centered position, and then cut off the 3 unneeded arms.  

5. Verify that the Link Clevises that attach to the servo arms are able to couple and rotate freely. Reaming each servo arm may be necessary, a value of 1.59mm (1/16 Inch, 62mil) is common.  

6. Route the servo wires through the conduit channels on the bottom of each wing to the main bay. Assuming all servos have a 6-inch (~150mm) pigtail, the Elevon servos will have some slack, but the Tilt servos will arrive just barely at the main bay. Servo Extensions can be added, or the servo pigtail can be extended with a section of 3-wire servo lead/cable, or the 3-pin servo connectors can be discarded in favor of direct soldering later if desired.  

7. With servo harnessing finished in one form or another, bond the servos to the airframe using Hot-Melt-Adhesive. Note that the airframe may exhibit deformation or melting at the bonding locations, depending on print material used. (This is acknowledged as a somewhat terrible way to mount servos, and will likely be revised in the future. Sorry.) Verify that the servos can produce full torque without becoming detached from the airframe. Also note that alternatives may be explored in servo mounting, such as double-sided adhesive tape, but it is not advised to use cyanoacrylate or epoxy.  

8. Form the elevon control rods by creating an L-bend 45mm from the threaded tip of the pair of 2-56 link rods used. Test fit the retaining Du-Bro E/Z Links 0.72 (2-56) Retainer Clip for each bend, and modify the bend as needed and cut flush. Alternatively, a traditional Z-bend can be formed to dismiss the Retain Clips as a requirement. For each Elevon, attach its control rod to the elevon control horn, and attach the clevis to the corresponding servo arm. Detach, turn the clevis, and reattach as needed until the elevon is flush while the servo is centered on 1500us.  

9. Cut two (2) 70mm long pieces from a fully-threaded 2-56 rod to form the tilt control rod pair. (DO NOT L-bend or Z-bend these rods.) Soften the cut ends with a grinder or emery wheel such that they will easily thread into the Nylon Ball-Link couplers. Thread on the ball-link couplers and link clevises, and attach each to its respective servo arm or ball-link head. Detach-turn-reattach as needed, such at the servo approaches as close to top-dead-centre (arm retracted into well/slot) as possible, without binding or interference, while the tilting motor mount is firmly forward and pressed against the nacelle. As noted earlier, the clevis should attach to the highest hole in the servo arm, at 19.3mm arm distance. It may be required to bend this rod slightly to allow for the servo arm to fully retract without the clevis impacting the arm. If the servo is straining excessively when the motor mount is retracted, adjust accordingly. **WARNING!** If the servo is allowed to strain with the clevis binding against the servo arm, the servo will likely fail, via burnt-out servo H-bridge driver, or burnt-out servo motor. Be careful and kind to the servos.  

10. The above steps assumed that the servos were powered and commanded during final installation, but for completeness, this step verifies that the servos are able to actuate, and are not being stressed. For each servo, visit 1000us-1500us-2000us and observe deflection on Elevons or Motor Mount and verify that there is no excessive binding or stress. For each motor mount, simulate the load exhibited during forward flight by gently pulling on the motor in the forward direction (about 300 grams force), while the servo is actively commanded to tilt between forward-flight and hover. The movement should be smooth and free of freezing/halting behavior. The elevons should actuate the full range with light loading on the control surface.

## Part 3 - Electronics and Final Configuration 
1. Solder the Flight Controller as desired. This usually means soldering pin headers to attach the 3-pin servo connectors from the servos and ESCs. Solder a battery connection lead (XT60 or as desired). Power the Flight Controller and verify that it is booting and communicating correctly. Default (likely multicopter) firmware will be fine for the next few steps; be advised that servos **SHOULD NOT** be connected to the flight controller until the flight controller outputs are configured.  

2. Bond the Battery and Flight Controller Trays into the main bay. This can be accomplished using M3 hardware and ample Hot-Melt-Adhesive and some reaming if necessary. The Battery Tray can be permanently mounted, but retain some ability to remove the Flight Controller Tray, as mounting/removing the flight controller requires access to the bottom of that tray. Also note: If using the ["Leaf-Spring" Flight Controller Tray](/stl-SourceFiles/MH7_ControllerTray2.stl), this should have about 30g to 40g of ballast weight attached to the underside of where the flight controller will be mounted. Self-adhesive lead weights work well. The reason for the ballast is to drive the corner frequency of the vibration transfer function well below 20 Hz or so. Also note that the compliant "Leaf Spring" mechanism can manifest harmonic vibration modes if used as-is, and it may be necessary to improvise a viscoelastic dampening solution, such as by injecting Hot-melt adhesive between the folds in the zig-zags, for example.  

3. Solder the BLDC Motor leads to each respective ESC, or use bullet-connectors or otherwise as desired. Solder the ESC power connections directly to the Flight Controller's Power-Distribution region, or to intermediate connections as desired. Remove the propellers from the motors. Power on the Flight Controller carefully, such as with a "Smoke Stopper" or a current-limited power supply, and verify that the power system is wired correctly. Program the ESCs for proper rotation direction: Port/Left Motor is Clockwise (CW), Starboard/Right Motor is Counterclockwise (CCW). (If using a BLHeli Passthru mode to program ESCs, the ESCs may be connected to any output(s) on the flight controller.) The Rear Motor may technically be either direction, but I **strongly** recommend Counterclockwise (CCW). This is a self-tightening configuration, so it is unlikely to unscrew itself in normal operation. This also allows for most non-multicopter propeller options (most propellers are CCW), and to force a consistent tradition that allows for future sharing of PID profiles and control schemes symmetrically. [Figure-15]
 > A brief note on prop rotation directions: The reason for the front motors having the Clockwise and Counterclockwise directions as stated is such that when the vehicle is flying in forward flight, and then immediately commanded to hover, the advancing blade(s) are placed as far abeam (toward the wingtip) as possible, while the retreating blade is closer to the main body. This should allow for better roll control through the transition, and by placing the effective centeres of lift for each rotor slightly wider in this condition, any PID control effort is more likely to remain bounded and slightly attenuated by the slightly longer moment-arm. This also follows the typical configuration for quadrotors, which also have the front advancing blades placed on the outside of the arc.  

4. At this point, configure the Flight Controller with any specific firmware or settings relevant to controlling a Tricopter VTOL Fixed-Wing vehicle. See [ArduPlane Settings](arduplane-brief) below. Attach the servo and ESC headers to their required pins. Install the R/C receiver and connect to the Flight Controller as required. Mount the Flight Controller to its tray, and secure the tray inside the main bay. Power the vehicle and verify Flight Controller orientation is correct, servos are properly commanded, and that control surface efforts are in the correct direction. Reverse and trim servo outputs as necessary in the Flight Controller configurator (ArduPilot Mission Planner or equivalent).  

5. (Optional) WS2812 LEDs may be mounted in each wingtip, provided each is a SMD5050 or smaller package, with wires directly soldered to the package pads, and then mounted in the light well on each tip.  

6. Stow the ESCs to the side-walls of the main bay using tape or double-sided adhesive pads. Stow any excess wires, and generally clean up the inside of the main bay. Secure the battery using Velcro straps, Tape, or other measures.  

7. Mount the propellers back onto to their respective motors. Verify that the rotation directions are correct, as described above in Step 3 and per [Figure-15]. The rear propeller should have had its tips trimmed slightly if it was necessary to avoid contacting the vertical fins.  

8. The Center-of-Mass for the aircraft is intended to be 28mm back from the leading edge of the wing. This is 2mm ahead of the proximate tray mounting holes. The centers of the "Bull's-eye" tactile mounds on the bottom of the wings near the nose are at 28mm. This is an essential metric, and the Center-of-Mass may only be shifted back up to 2mm or 3mm from this point, but with increasing risk to stability. The aircraft will NOT fly statically stable with the CG aft of ~33mm, as the neutral point resides near this point. The Center-of-Mass should be between 26mm and 30mm back from the wing leading edge. Use the Weight-and-Balance Stand and a digital scale, as detailed here: [Issue #12](https://github.com/StephenCarlson/MiniHawk-VTOL/issues/12#issuecomment-828814266) As this vehicle is both a fixed-wing and multicopter, the Center-of-Mass stated here is for the fixed-wing condition, and any measurement of Center-of-Mass should be performed with the motors tilted into the forward-flight condition, with propellers attached, and the lid secured. Shift the battery fore or aft to achieve proper balance, or add ballast inside the tip of the nose if merited. [Figure-16]  

9. Perform any other measures necessary to get the vehicle ready for flight. Decals, paint, or heat-activated covering are possibilities. Vehicle mass should come to an All-Up-Weight around 1000 grams to 1200 grams, with the 3D-printed airframe alone measuring around 460 grams if printed with standard PLA.  

<table style="width:100%">
  <tr>
    <td><figure>
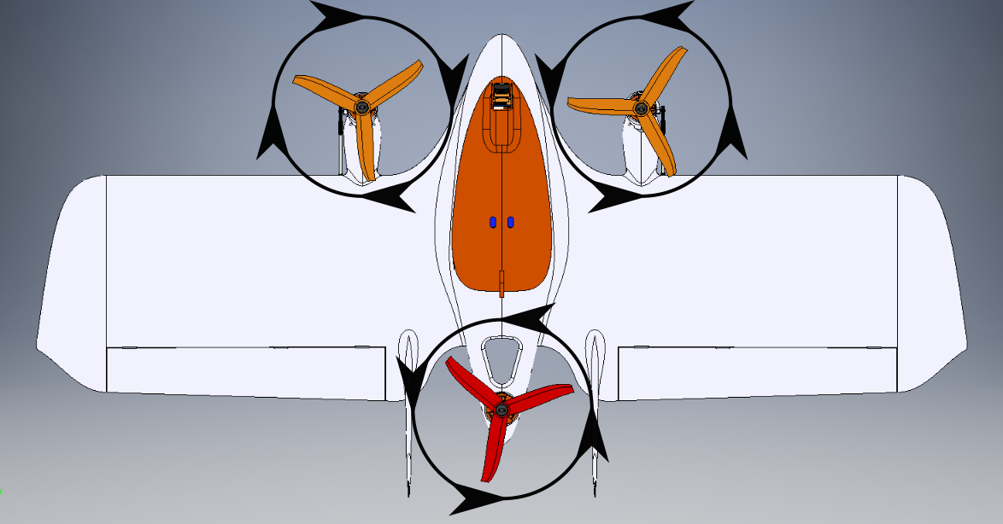
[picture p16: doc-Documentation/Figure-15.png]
      <br>
      <figcaption>Figure 15. Propeller Rotation Directions</figcaption></figure></td>
    <td><figure>
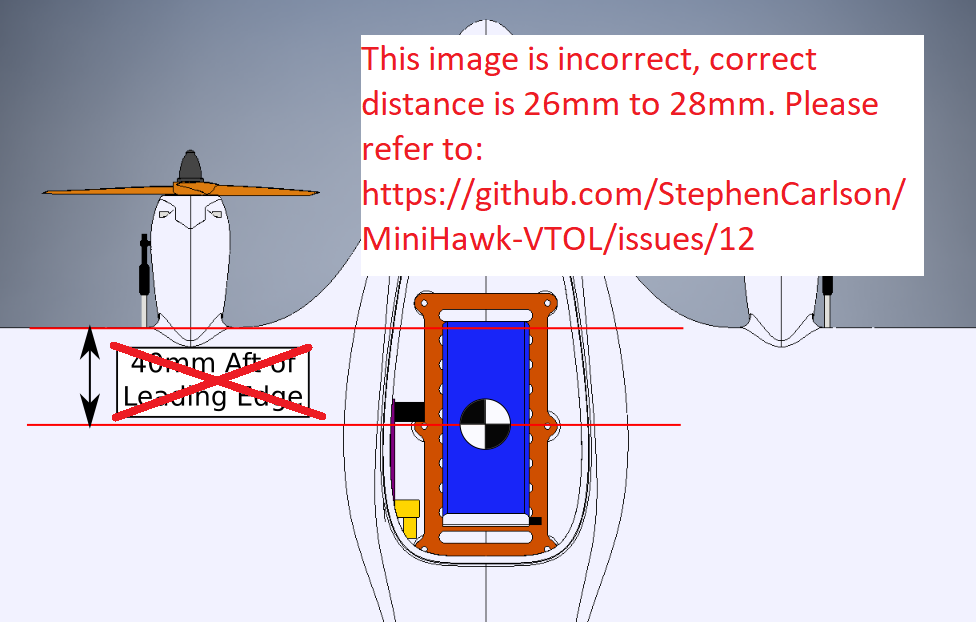
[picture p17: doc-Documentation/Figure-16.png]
      <br>
      <figcaption>Figure 16. Center of Mass</figcaption></figure></td>
  </tr>
</table> 

# Flight Testing 
The clean-sheet approach to tuning this vehicle for flight roughly follows this sequence of steps:
1. Discover the hovering-flight PIDs. This can be done using a test-stand setup and axis-isolation of roll, pitch and yaw. Gain Scheduling for hover-to-forward-flight and reverse transitions can also be performed with a pitch-isolated configuration, but relevance diminishes for angles approaching forward-flight without equivalent relative wind generation. (ArduPlane does this calculation intrinsically, implementing VTOL to other flight-stacks may require developing the Gain Schedule Table.)  

2. Continue PID tuning until free hovering hops and static hovering are demonstrated. Tune the position-hold behaviors and demonstrate autonomous Return-to-Land functionality. Demonstrate robust upset recovery and stability. Tune the weathervane behavior until satisfactory.  

3. Confirm Weight-and-Balance of the aircraft (26mm to 30mm from the wing leading edge). Verify that pitch is statically stable at cruising speed (19 m/s). Also verify that the aircraft is directionally stable (static weathervaning). Trim the pitch on the elevons to produce a level glide at 19 m/s.  

4. Confirm that the control surface deflections are correct for both pilot inputs and autopilot stabilization responses to aircraft movement and pose. Reduce forward-flight PIDs substantially if merited. Hand-launch the aircraft into forward-flight and confirm that it is controllable and stable. Beware that if control throws are too large, the controls can be very responsive and fast. Exit from fixed-wing flight to hover and land safely.  

5. If the aircraft is still intact and functional from the previous step, perform AUTOTUNE or equivalent to arrive at sensible PIDs for forward-flight. Tune the waypoint following behaviors and demonstrate consistent navigation. If applicable, demonstrate autonomous landing starting from fixed-wing flight.  

6. Hover-climb to at least 50 meters and attempt forward-flight VTOL transitions. Tune the transition behavior until the vehicle consistently enters forward-flight. Transitions should look the same for both human-piloted and autonomous cases.
> The vehicle is designed to hover with a nose-high attitude (positive Angle-of-Attack). The reason for this is so that as the nose is dropped to level, the thrust vector brings the vehicle to an initial forward drift. Having established a forward trajectory, the motors are tilted to the 50/50 intermediate point and the vehicle is allowed to accelerate. The motors are then dropped to full forward-flight position.
8. Demonstrate full autonomous missions from launch to landing with forward- and reverse-transition behaviors.

# 3D Printing Guidelines 
Unlike other 3D-printed R/C aircraft, the MiniHawk does not have any internal structures explicitly specified, such as ribs or stringers; only the outer-mold-line of the aircraft and the bays, wiring conduits, and mounting points are defined. The internal structure is yielded to whatever infill pattern is selected in the slicing software used to convert the volume definition for 3D-Printing. The internal structures may be explicitly defined in a future revision, but otherwise it is up to the builder to define the infill pattern used. The following sections provide recommended settings for each airframe part set (matching the settings in the 3MF files).

| Parameter | Left and Right Wings | Nose | Empennage | Hatch/Lid | Nacelles | Motor Tilt Mounts |
|---|---|---|---|---|---|---|
| LayerHeight | 0.2mm | 0.2mm | 0.2mm | 0.2mm | 0.2mm | 0.2mm |
| WallThickness | 0.4mm | 0.4mm | 0.4mm | 0.4mm | 0.8mm | 0.8mm |
| TopThickness | 0.2mm | 0.2mm | 0.2mm | 0.2mm | 0.6mm | 0.6mm |
| BottomThickness | 0.2mm | 0.2mm | 0.2mm | 0.2mm | 0.6mm | 0.6mm |
| TopBottomMainPattern | Lines | Concentric | Lines | Lines | Lines | Lines |
| InitialBottomLayerPattern | Concentric | Concentric | Concentric | Concentric | Lines | Lines |
| FillGapsBetweenWalls | Nowhere | Nowhere | Nowhere | Nowhere | Everywhere | Everywhere |
| Z-SeamAlignment | UserSpecified (Note 1) | SharpestCorner,HideSeam | SharpestCorner,HideSeam | SharpestCorner,HideSeam | SharpestCorner,ExposeSeam | SharpestCorner,ExposeSeam |
| InfillDensity | 5.00% | 10.00% | 10.00% | 10.00% | 20.00% | 30.00% |
| InfillPattern | Cubic | Cubic | Cubic | Cubic | Cubic | Cubic |
| InfillLineDirections | 90deg | 0deg | 0deg (Note 2) | 90deg | 0deg | 0deg |
| GenerateSupport | Nowhere | Nowhere | Nowhere | Nowhere | Yes | Nowhere |
| SupportPlacement | | | | | TouchingBuildPlate | |
| SupportOverhangAngle | | | | | 70deg | |
> Note 1: Forced to occur on trailing edge of wing.  
> Note 2: Is slightly offset in X-direction for best structure.  

For the MH7_ControlHornSet and MH7_TraySet, print 100% Solid or as desired. These pieces may be laser-cut if possible.

# ArduPlane Settings 
While the MiniHawk-VTOL initially was developed using the BetaFlight avionics ecosystem, ArduPilot is the reccomended ecosystem for the current design. This text section replaces the original Betaflight setup instructions which existed in this section prior to v2.0.0. The old Betaflight setup instructions can be found in the README.md file revision history.

## R/C Controller Configuration (Mode 2 Controller) 
| R/C Channel | Description | 1000us | 1500us | 2000us | Notes |
|---|---|---|---|---|---|
| CH 1 | Roll | Roll Left | Centered | Roll Right | |
| CH 2 | Pitch | Nose Up | Neutral | Nose Down | |
| CH 3 | Throttle/Collective | Idle | 50% Thrust | 100% Thrust | Be careful switching between QSTABILIZE and QLOITER/QHOVER |
| CH 4 | Rudder | Yaw Left | Neutral | Yaw Right | |
| CH 5 | Flight Mode Select  | FBWA | QSTABILIZE | AUTO/RTL/AUTOTUNE | 3-Position Switch, 2000us is formed by mixing a 2nd R/C switch |
| CH 6 | MANUAL Override | Disabled | --- | MANUAL Mode ACTIVE! | RC6_OPTION=51, useful for hand-launching into forward-flight |
| CH 7 | Arming Switch | Disabled | --- | ARMED! | RC7_OPTION=41, ArduPilot Arming/Disarming Switch |
| CH 8 | Momentary Switch | Disabled | --- | OSD, Inverted Mode, etc | OSD Screen Cycling, Inverted (RC8_OPTION=43), other misc uses  |

Note that MANUAL Mode is a real handful, and should only be used rarely. It is included above as a kind of "cheat" to force the ArduPlane VTOL state-machine to stay in Forward-Flight when Arming, such as when you want to hand-launch the aircraft to skip the VTOL hover and forward transition. First set the aircraft to FBWA using the CH 5 Flight Mode Select Switch, and then turn on the MANUAL Override switch only for a moment and then back to disabled (Flight mode returns to FBWA as set by the Flight Mode switch). Otherwise, if you only select FBWA and then arm, the aircraft immediately reverts to the ArduPlane VTOL forward transition behavior with all three motors spinning in the hover condition.

## Flight Controller Connections 
The following table works on the mRobotics PixRacer Pro. This should be adapted to whatever ArduPlane-compatible flight controller is otherwise used.

| Pin # | Control Endpoint |
|---|---|
| S1 | Right Motor ESC |
| S2 | Left Motor ESC |
| S3 | NO CONNECTION (BEC) |
| S4 | Rear/Tail Motor ESC |
| S5 | Left Tilt Servo |
| S6 | Right Tilt Servo |
| S7 | Left Elevon Servo |
| S8 | Right Elevon Servo  |

## ArduPlane Parameters 
The parameters file below represents the settings used on a typical MiniHawk-VTOL utilizing a mRo PixRacer Pro flight controller. The essential settings should be applicable to whatever ArduPlane-compatible flight controller is used, such as the Matek F405-WING or similar, but some adaptation will be required. **WARNING!** Modern ESC protocols (such as OneShot or DShot) do not play well with servos if accidentally connected. At best, the servo will filter out the packet, but in some cases the servo will burn out. Don't plug servos into the ESC outputs!

mRo PixRacer Pro: [ArduPlane_MiniHawk_mRo_PixRacerPro.param](/cfg-Config/ArduPlane_MiniHawk_mRo_PixRacerPro.param)

While the parameters file above has over 1100 parameters, some essential parameters are examined below:
```
| Parameter,Value        | Notes                                                      |
| ---------------------- | ---------------------------------------------------------- |
| ARSPD_FBW_MAX,32       | Full-Throttle produces around 32 to 34 m/s sprint velocity |
| ARSPD_FBW_MIN,17       | Stall is near 15 m/s for a typical MiniHawk-VTOL           |
| ARSPD_RATIO,1.9936     | Make sure this is calibrated for your aircraft             |
| ARSPD_TUBE_ORDER,0     | While this can be automatic (3), manually set is better    |
| ARSPD_TYPE,1           | MS4525D0 Pressure Sensor, adjust as needed                 |
| ARSPD_USE,1            | Force the aircraft to use the pitot probe, no synthetic    |
| AUTOTUNE_LEVEL,7       | 7 or 8 works best for the MiniHawk-VTOL                    |
| EK2_ENABLE,0           | EKF2 is Disabled, in favor of EKF3                         |
| EK3_ENABLE,1           | EKF3 was used for most flight testing of the design        |
| FLTMODE_CH,5           | Flight Mode Channel                                        |
| FLTMODE1,5             | FBWA, 3-position switch "Down" detent                      |
| FLTMODE2,19            | QLOITER, 3-position switch "Middle" detent                 |
| FLTMODE3,17            | QSTABILIZE, 3-position switch "Up" detent                  |
| FLTMODE4,17            |                                                            |
| FLTMODE5,17            |                                                            |
| FLTMODE6,10            | AUTO, 2nd R/C switch that overrides the 3-position switch  |
| FS_LONG_ACTN,1         | Failsafe Settings used in development                      |
| FS_LONG_TIMEOUT,3      |                                                            |
| FS_SHORT_ACTN,1        |                                                            |
| FS_SHORT_TIMEOUT,1     |                                                            |
| KFF_RDDRMIX,0          | Remove any possible rudder mixing                          |
| LIM_PITCH_MAX,2000     | Pitch and Roll Angle Limits                                |
| LIM_PITCH_MIN,-2500    |                                                            |
| LIM_ROLL_CD,5500       |                                                            |
| MIXING_GAIN,0.5        | Elevon Stick Mixing, value here should be default          |
| NAVL1_PERIOD,11        | More aggressive navigation is possible, 11 to 14 tested    |
| PTCH_RATE_D,0          | Pitch PIDs, these values are mild, AUTOTUNE will increase  |
| PTCH_RATE_FF,0.345     |                                                            |
| PTCH_RATE_FLTD,4       |                                                            |
| PTCH_RATE_FLTE,7       |                                                            |
| PTCH_RATE_FLTT,1.5     |                                                            |
| PTCH_RATE_I,0.15       |                                                            |
| PTCH_RATE_IMAX,0.666   |                                                            |
| PTCH_RATE_P,0.04       |                                                            |
| PTCH_RATE_SMAX,150     |                                                            |
| PTCH2SRV_RLL,1         |                                                            |
| PTCH2SRV_RMAX_DN,90    |                                                            |
| PTCH2SRV_RMAX_UP,90    |                                                            |
| PTCH2SRV_TCONST,0.4    |                                                            |
| Q_A_ACCEL_P_MAX,110000 | VTOL R/P/Y Angular accelerations used in development       |
| Q_A_ACCEL_R_MAX,110000 |                                                            |
| Q_A_ACCEL_Y_MAX,27000  |                                                            |
| Q_A_RAT_PIT_D,0.0005   | VTOL Pitch PIDs                                            |
| Q_A_RAT_PIT_FF,0       |                                                            |
| Q_A_RAT_PIT_FLTD,15    |                                                            |
| Q_A_RAT_PIT_FLTE,0     |                                                            |
| Q_A_RAT_PIT_FLTT,20    |                                                            |
| Q_A_RAT_PIT_I,0.15     |                                                            |
| Q_A_RAT_PIT_IMAX,0.5   |                                                            |
| Q_A_RAT_PIT_P,0.15     |                                                            |
| Q_A_RAT_PIT_SMAX,0     |                                                            |
| Q_A_RAT_RLL_D,0.003    | VTOL Roll PIDs                                             |
| Q_A_RAT_RLL_FF,0       |                                                            |
| Q_A_RAT_RLL_FLTD,15    |                                                            |
| Q_A_RAT_RLL_FLTE,0     |                                                            |
| Q_A_RAT_RLL_FLTT,20    |                                                            |
| Q_A_RAT_RLL_I,0.25     |                                                            |
| Q_A_RAT_RLL_IMAX,0.5   |                                                            |
| Q_A_RAT_RLL_P,0.45     |                                                            |
| Q_A_RAT_RLL_SMAX,0     |                                                            |
| Q_A_RAT_YAW_D,0.02     | VTOL Yaw PIDs                                              |
| Q_A_RAT_YAW_FF,0.1     |                                                            |
| Q_A_RAT_YAW_FLTD,0     |                                                            |
| Q_A_RAT_YAW_FLTE,10    |                                                            |
| Q_A_RAT_YAW_FLTT,20    |                                                            |
| Q_A_RAT_YAW_I,0.1      |                                                            |
| Q_A_RAT_YAW_IMAX,0.5   |                                                            |
| Q_A_RAT_YAW_P,0.6      |                                                            |
| Q_A_RAT_YAW_SMAX,0     |                                                            |
| Q_ANGLE_MAX,3000       | VTOL Pitch and Roll Angle Limits                           |
| Q_ASSIST_ALT,0         | Disable VTOL Assist where possible                         |
| Q_ASSIST_ANGLE,0       |                                                            |
| Q_ASSIST_DELAY,0.5     |                                                            |
| Q_ASSIST_SPEED,0       |                                                            |
| Q_AUTOTUNE_AGGR,0.1    | VTOL Autotune settings used in development                 |
| Q_AUTOTUNE_AXES,2      |                                                            |
| Q_AUTOTUNE_MIN_D,0.001 |                                                            |
| Q_ENABLE,1             | VTOL obviously is enabled for the MiniHawk-VTOL            |
| Q_FRAME_CLASS,7        | Tricopter Configuration                                    |
| Q_FW_LND_APR_RAD,85    | 85 meters for Fixed-wing to VTOL threshold                 |
| Q_M_HOVER_LEARN,2      | Hover throttle setpoint learning                           |
| Q_M_PWM_TYPE,4         | DShot 150 is sufficient and noise-resistant                |
| Q_M_SPIN_ARM,0.05      | 5% Throttle when armed                                     |
| Q_M_SPIN_MAX,1         | 100% Throttle max ESC RPM command                          |
| Q_M_SPIN_MIN,0.1       | 10% Throttle for lowest ESC RPM                            |
| Q_M_SPOOL_TIME,0.5     | 500ms spool time                                           |
| Q_M_THST_EXPO,0.25     | Throttle Expo                                              |
| Q_M_YAW_HEADROOM,50    | 50us Yaw Headroom                                          |
| Q_M_YAW_SV_ANGLE,12    | "12" Degrees for Yaw lean angle                            |
| Q_OPTIONS,1056         | Allow yaw actuation when disarmed, QRTL behavior           |
| Q_RC_SPEED,490         | 490 Hz Motor Updates                                       |
| Q_RTL_ALT,40           | RTL Behaviors in VTOL                                      |
| Q_RTL_MODE,1           |                                                            |
| Q_TILT_MASK,3          | Which motors are being tilted                              |
| Q_TILT_MAX,55          | Transition angle while AirspeedWait is active              |
| Q_TILT_RATE_DN,15      | Tilt Up/Down rates                                         |
| Q_TILT_RATE_UP,75      |                                                            |
| Q_TILT_TYPE,2          | Vectored Yaw Tilt Type                                     |
| Q_TILT_YAW_ANGLE,14    | "14" degrees VTOL hover position                           |
| Q_TRANS_FAIL,0         | Transition Timeout is disabled                             |
| Q_TRANSITION_MS,1000   | Post-transition wait period                                |
| Q_TRIM_PITCH,9         | Pitch offset between forward-flight and hover stance       |
| Q_WVANE_GAIN,0.4       | 0.4 is a good value for this design                        |
| RC7_OPTION,41          | Arming Switch, will disable motors if in flight/hover!     |
| RCMAP_PITCH,2          | Roll/Pitch/Throttle/Yaw (AETR) controls ordering           |
| RCMAP_ROLL,1           |                                                            |
| RCMAP_THROTTLE,3       |                                                            |
| RCMAP_YAW,4            |                                                            |
| RLL_RATE_D,0           | Roll PIDs, these values are mild, AUTOTUNE will increase   |
| RLL_RATE_FF,0.345      |                                                            |
| RLL_RATE_FLTD,4        |                                                            |
| RLL_RATE_FLTE,7        |                                                            |
| RLL_RATE_FLTT,3        |                                                            |
| RLL_RATE_I,0.15        |                                                            |
| RLL_RATE_IMAX,0.666    |                                                            |
| RLL_RATE_P,0.08        |                                                            |
| RLL_RATE_SMAX,150      |                                                            |
| RLL2SRV_RMAX,90        |                                                            |
| RLL2SRV_TCONST,0.4     |                                                            |
| RTL_AUTOLAND,2         | Fixed-wing to VTOL landing behavior in RTL                 |
| RUDD_DT_GAIN,3         | Very mild differential thrust mixing on forward motors     |
| SCALING_SPEED,15       | 15 m/s should be default                                   |
| SCHED_LOOP_RATE,300    | 300 Hz was used in development                             |
| SERVO1_FUNCTION,33     | Right BLDC Motor                                           |
| SERVO2_FUNCTION,34     | Left BLCD Motor                                            |
| SERVO3_FUNCTION,0      | No Connection, 5V BEC connected here for mRo PixRacer Pro  |
| SERVO4_FUNCTION,36     | Rear BLCD Motor                                            |
| SERVO5_FUNCTION,75     | Left Tilt Servo                                            |
| SERVO5_MAX,1800        | MAX and MIN values are hand calibrated, close to 1920/1080 |
| SERVO5_MIN,1200        | Values of 1200/1800 here to prevent damage on new builds   |
| SERVO5_REVERSED,0      | Left Tilt is normal rotation direction                     |
| SERVO6_FUNCTION,76     | Right Tilt Servo                                           |
| SERVO6_MAX,1800        |                                                            |
| SERVO6_MIN,1200        |                                                            |
| SERVO6_REVERSED,1      | Right Tilt is reversed rotation direction                  |
| SERVO7_FUNCTION,77     | Left Elevon Servo                                          |
| SERVO7_REVERSED,1      | Left Elevon is reverse rotation direction                  |
| SERVO8_FUNCTION,78     | Right Elevon Servo                                         |
| SERVO8_REVERSED,0      | Right Elevon is normal rotation direction                  |
| STAB_PITCH_DOWN,2      | 2 should be default, pitch behavior on zero-throttle       |
| STALL_PREVENTION,0     | May be enabled, was disabled for development               |
| STICK_MIXING,1         | How pilot inputs are fused in autonomous modes             |
| TECS_PTCH_FF_V0,19     | 19 m/s cruise                                              |
| TRIM_ARSPD_CM,1900     | 19 m/s cruise                                              |
| TRIM_PITCH_CD,350      | Offset between level-flight pitch angle and tray angle     |
| TRIM_THROTTLE,55       | Typical 19 m/s cruise throttle                             |
| WP_LOITER_RAD,60       | 60 meter radius for loiter typical                         |
| WP_RADIUS,40           | 40 meter waypoint radius typical                           |
```

## Remarks: 
ArduPlane v4.1.0 and v4.2.0dev were used in the development of the Version 2 MiniHawk-VTOL. "Out-of-the-box", ArduPlane has support for a Tricopter Tiltrotor such as this design, and only the parameters need to be set for enabling the VTOL behaviors. 

At this firmware version, there are some aspects of how VTOL flight behaviors are handled which are somewhat counter-intuitive. The most annoying of these is that for both piloted and autonomous flying, there is no direct control of the VTOL flight state. Instead of being able to directly command the Forward-Flight condition, the VTOL state-machine requires an airspeed estimate (either synthetic or measured from a pitot probe) to drive the forward VTOL transition to fixed-wing flight. This makes the human pilot merely a voting member in the transition process, with accumulated airspeed determining when the tilting rotors are allowed to fully tilt forward and the rear motor to halt. The developers' mentality treats the hover condition as the default fallback, and any failure to accumulate airspeed in a certain amount of time will have the process revert to hover as a failsafe via `Q_TRANS_FAIL`. If this transition failure timeout is disabled, the AirspeedWait state will persist and the vehicle will fly in a half-way blend between tricopter and fixed-wing flight indefinitely. For a vehicle design such the MiniHawk-VTOL, over-powered and very fast, it would make more sense for a timeout to result in forcing forward-flight rather than to place the vehicle in this blended behavior, or if using the transition failure timer, to place the vehicle into hover with limited battery at extreme range and altitude, but that is a pull request for another day. And thus, for the current firmware state, it is necessary to be aware of this behavior and to know why it gets stuck in the blended mode.

Another consequence of the forward-transition VTOL behavior is that while disarmed, even though a forward-flight mode selection (such as FBWA) will result in the rotors tilting to the forward position, upon arming, the vehicle will immediately assume the AirspeedWait state, with the front rotors tilting up and the rear rotor spinning up. The throttle setting apparently determines the mix between hovering and forward-flight airspeed wait, but a better solution if you are trying to hand-launch like a traditional fixed-wing is to "bump" into MANUAL mode for a moment. This forces the VTOL state-machine past the AirspeedWait state and allows you to Arm in FWBA mode and have the forward rotors remain in the forward position and also enjoy elevon stabilization and leveling while hand-launching. Just be sure to flip out of MANUAL mode back to FBWA, unless you intend a fully MANUAL hand-launch with no stabilization or leveling.

Transitions from Fixed-Wing flight to hover are typically smooth when being human-piloted, but in autonomous modes, there is a known issue in which the vehicle will nose-dip and then pull up hard when making the reverse VTOL transition to hover. This can be hazardous to the vehicle if negative gee-loading or sudden jerk movement will cause parts to separate. The issue is likely in the TECS tuning parameters, or is an issue local to firmware 4.1 or 4.2.

# License 
This work is licensed under the Creative Commons Attribution-NonCommercial-ShareAlike 4.0 International License. To view a copy of this license, visit http://creativecommons.org/licenses/by-nc-sa/4.0/ or send a letter to Creative Commons, PO Box 1866, Mountain View, CA 94042, USA.  

The Ardupilot and Betaflight software configuration text files provided here likely fall under GPL-3.0; both projects are licensed under GPL-3.0 at the time of this writing.  

MiniHawk VTOL - Design, Documentation, Images and all other Artwork; by Steve Carlson  
[https://github.com/StephenCarlson/MiniHawk-VTOL](https://github.com/StephenCarlson/MiniHawk-VTOL)

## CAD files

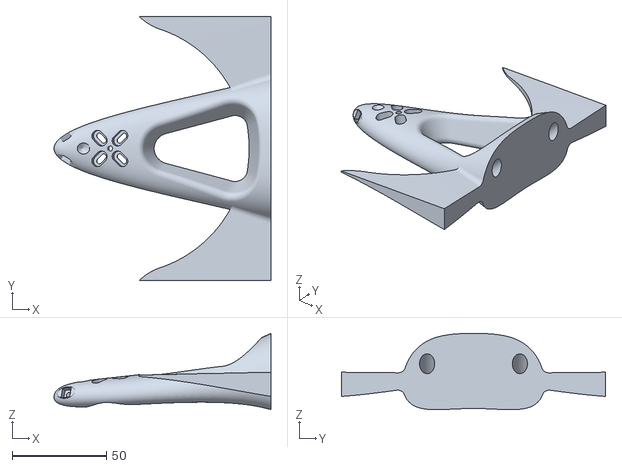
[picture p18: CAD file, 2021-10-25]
stl-SourceFiles/MH7_Empennage-Full.stl
115.0 x 140.0 x 40.5

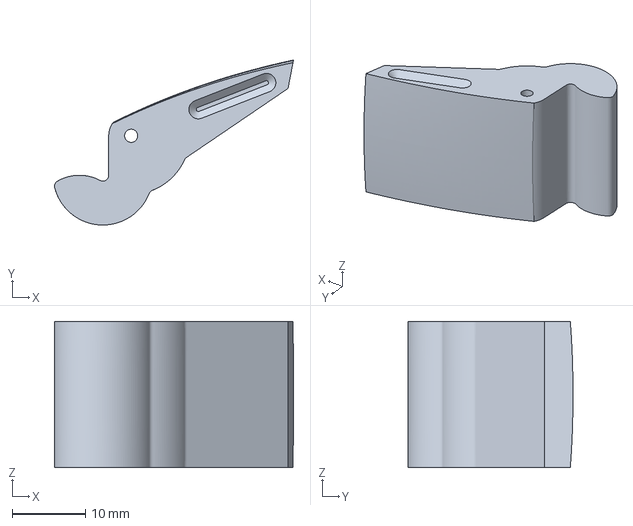
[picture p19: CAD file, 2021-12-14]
3mf-Implementations/MH7_Hatch_LockingLatch.3mf
32.7 x 22.6 x 20.0 mm

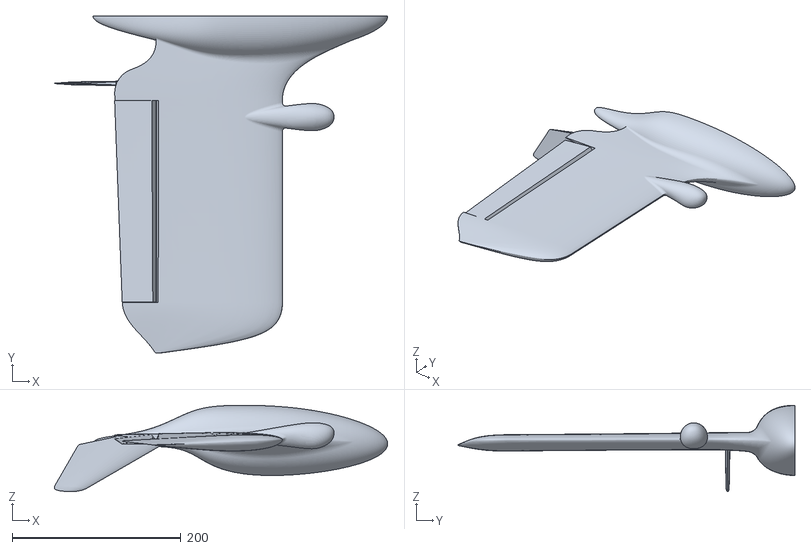
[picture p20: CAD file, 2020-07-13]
cfd-Analysis/MH5_CFD_u5deg.stl
395.8 x 400.0 x 102.5

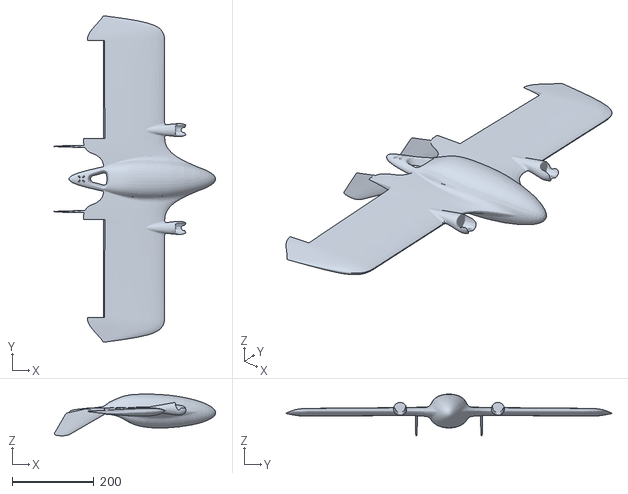
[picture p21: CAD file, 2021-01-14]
sim-ReducedGeometry/MH5_SimReduced_Airframe_BREP.stl
395.7 x 800.0 x 102.5

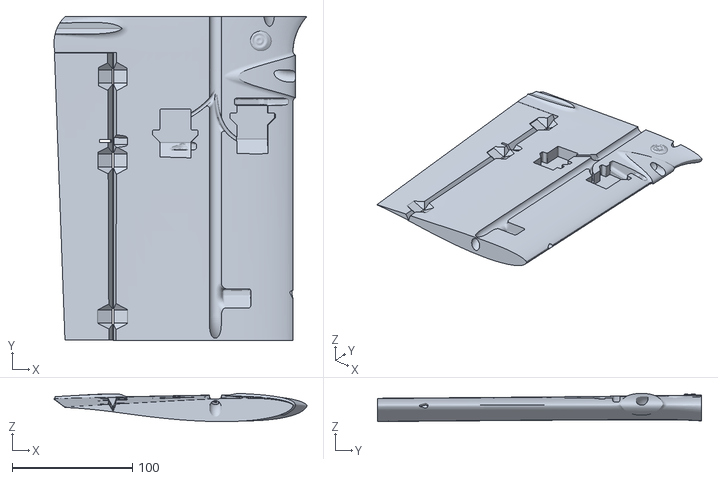
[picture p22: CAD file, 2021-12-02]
stl-SourceFiles/MH7_WingLeft.stl
210.7 x 270.0 x 23.5

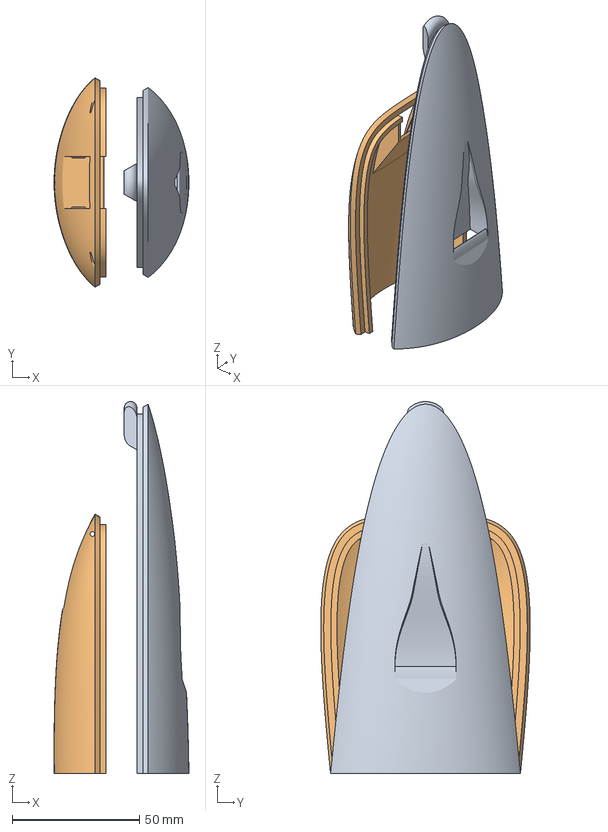
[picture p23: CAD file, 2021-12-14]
3mf-Implementations/MH7_Hatch-Vented_Set.3mf
52.9 x 82.2 x 146.0 mm

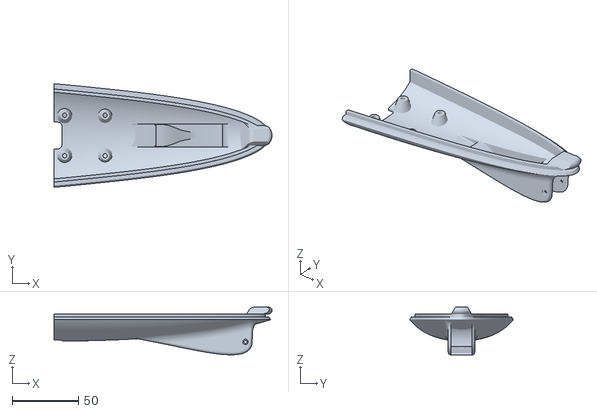
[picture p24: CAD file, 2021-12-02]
stl-SourceFiles/MH7_Hatch-FPV-16mm_a.stl
164.0 x 77.9 x 35.9

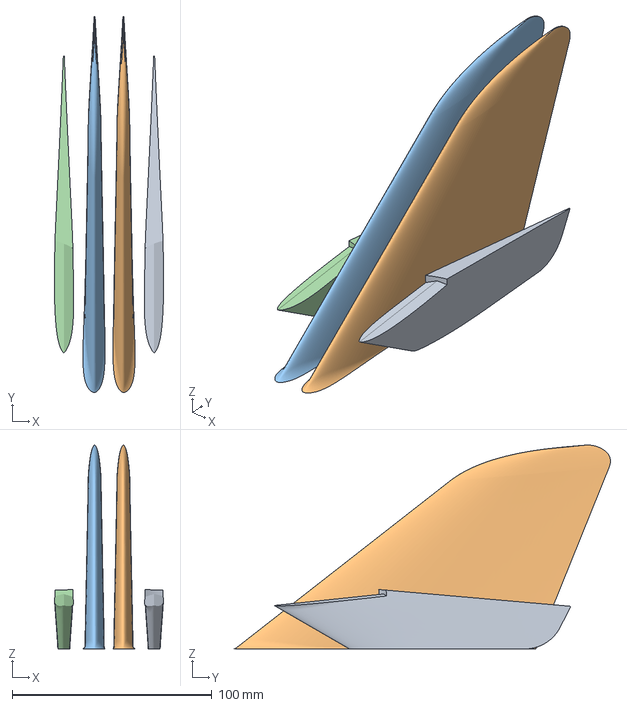
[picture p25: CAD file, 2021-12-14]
3mf-Implementations/MH7_Fin_Set.3mf
54.7 x 188.2 x 102.1 mm

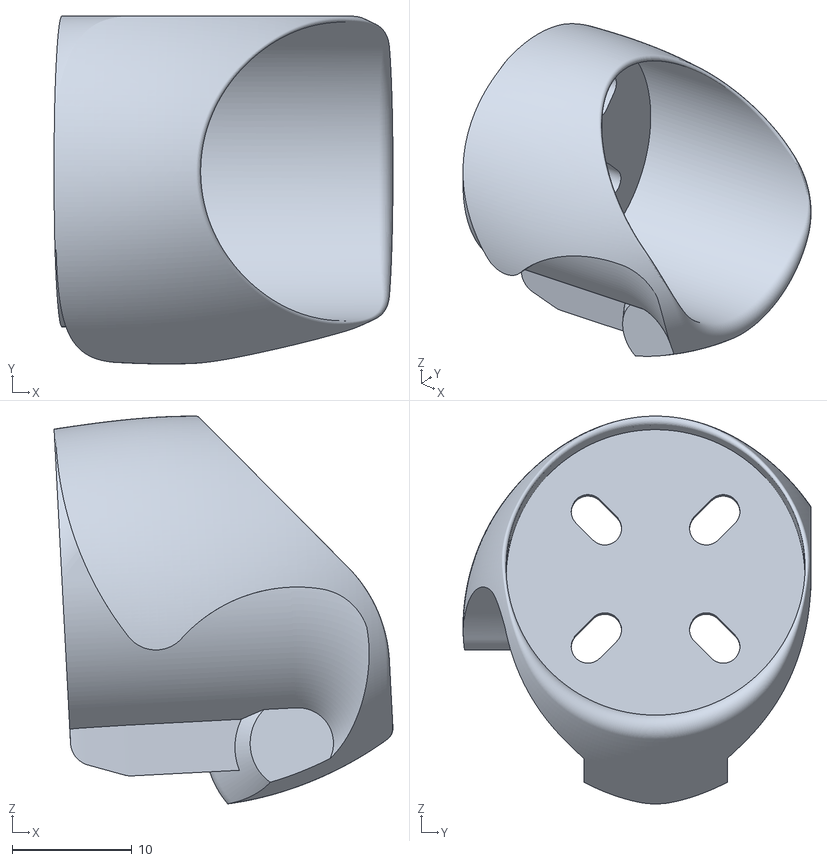
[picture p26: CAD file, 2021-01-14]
sim-ReducedGeometry/MH5_SimReduced_TiltMountLeft_LOD-0.stl
28.3 x 29.1 x 32.4

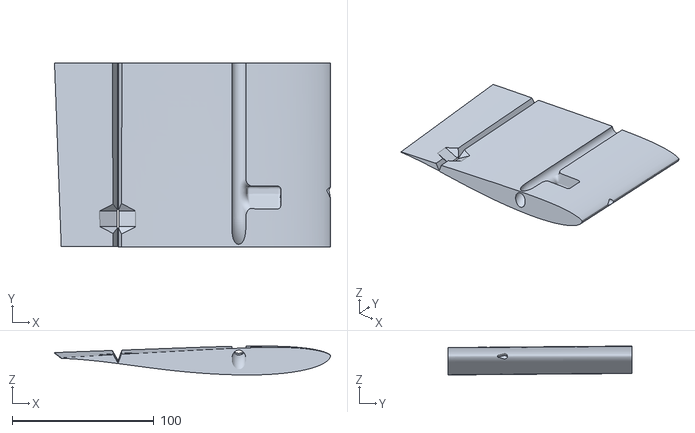
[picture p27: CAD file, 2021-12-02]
stl-SourceFiles/MH7_WingLeft_B.stl
194.8 x 130.0 x 20.5

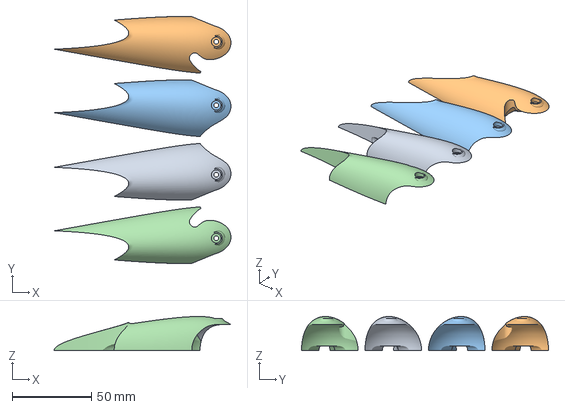
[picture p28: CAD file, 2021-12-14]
3mf-Implementations/MH7_Nacelle-Bearing_Set.3mf
111.5 x 155.6 x 21.4 mm

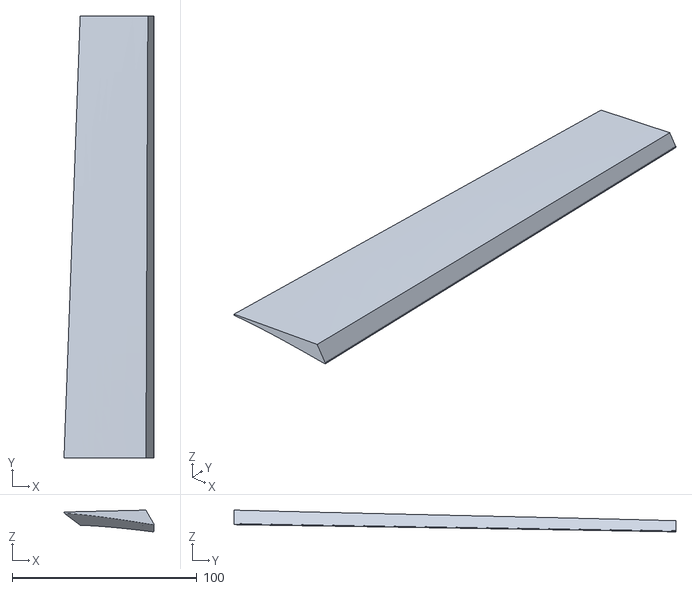
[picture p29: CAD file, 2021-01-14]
sim-ReducedGeometry/MH5_SimReduced_ElevonRight_LOD-2.stl
48.8 x 239.4 x 11.8

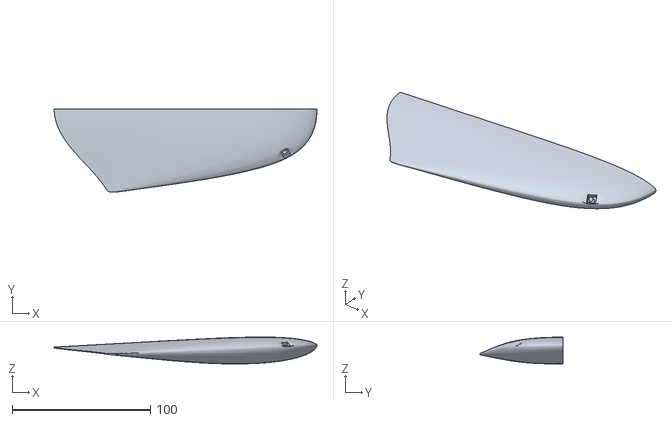
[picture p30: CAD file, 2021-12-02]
stl-SourceFiles/MH7_WingletLeft-GPS.stl
190.1 x 60.0 x 19.4

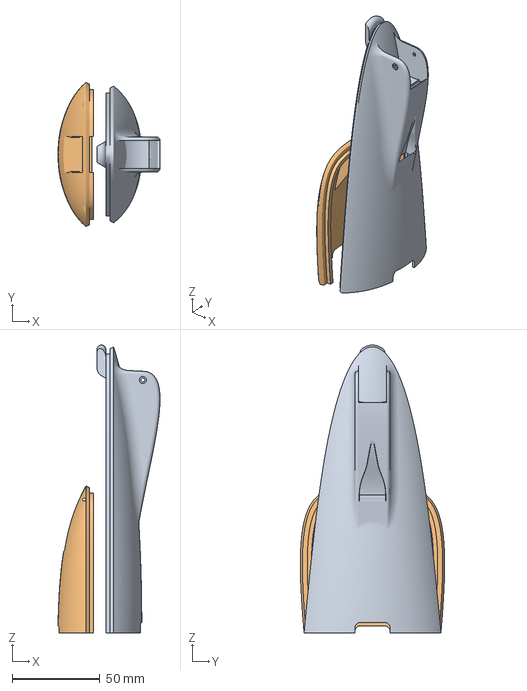
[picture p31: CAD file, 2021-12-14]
3mf-Implementations/MH7_Hatch-FPV_Set.3mf
58.1 x 82.2 x 164.0 mm

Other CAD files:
cfd-Analysis/MH5_CFD_d1deg.stl
sim-ReducedGeometry/MH5_SimReduced_Airframe_LOD-2.stl
cfd-Analysis/MH5_CFD_d7deg.stl
cfd-Analysis/MH5_CFD_d13deg.stl
3mf-Implementations/MH7_AvionicsTray2.3mf
3mf-Implementations/MH7_BatteryTray.3mf
3mf-Implementations/MH7_ControlHorn_Set.3mf
3mf-Implementations/MH7_Empennage_Set.3mf
3mf-Implementations/MH7_Hatch-GraspStub_Set.3mf
3mf-Implementations/MH7_MotorSpacer_Set.3mf
3mf-Implementations/MH7_Nacelle-NoBearing_Set.3mf
3mf-Implementations/MH7_Nose-NacaDucts.3mf
3mf-Implementations/MH7_Nose.3mf
3mf-Implementations/MH7_TiltMount-NoBearing_Set.3mf
3mf-Implementations/MH7_WeightBalanceStand_Set.3mf
3mf-Implementations/MH7_WingLeft-Solar.3mf
3mf-Implementations/MH7_WingLeft.3mf
3mf-Implementations/MH7_Winglet_Set.3mf
cfd-Analysis/MH5_CFD_0deg.stl
cfd-Analysis/MH5_CFD_clean-BREP.stl
cfd-Analysis/MH5_CFD_clean.stl
cfd-Analysis/MH5_CFD_d11deg.stl
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

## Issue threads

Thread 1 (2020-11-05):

Add Spar for Rigidity

StephenCarlson, 2020-11-05:
# Details
A carbon fiber spar should be added, likely intersecting the extreme rear of the main compartment. The main compartment may have the rear wall pulled forward such that the spar is submerged, or the spar can be exposed by retaining the current compartment geometry.

Ideally, the spar would be along the quarter-chord, but that would intersect with the battery. The OML would have to be altered to allow the spar to pass either above or below the battery, but if adding the spar along near the rear trailing edge of the wings is enough, then no need to rework the entire vehicle geometry.

StephenCarlson, 2021-04-28:
Solved by ede11e9. The spar may be up to 610mm long (24 inches), and the inside diameter is 7mm, supporting any round or square carbon rod or tube that is inside this diameter. (Example include 0.25 inch rod/tube, 6mm round rod/tube, 5mm square tube with rounded edges.) In my builds, I've used a 500mm long 5mm square tube, which is sufficient despite not filling the entire 610mm channel.

Closed 2021-04-28.

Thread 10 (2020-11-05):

Outboard Washout Angle reduced, possibly select alternate airfoil for tip.

StephenCarlson, 2020-11-05:
The washout from root-to-tip is fairly large, owing to this being my first plank design and my selecting a generous washout angle, which on some casual analysis is likely too much. Reducing this too far may result in tip-stalling and poor flight characteristics. The tip airfoil could also be swapped or altered.

This issue would require changes to the OML, v2.0.x required.

StephenCarlson, 2021-01-13:
Related to this, the the top wing surface should be made *geometrically developable* for future features to be announced.

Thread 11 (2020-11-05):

Nacelle Motor Wire Containment and Motion Fixes

StephenCarlson, 2020-11-05:
The current v1.0.x motor nacelle design allows for the motor wires to be scrunched into a bundle pocket as the motor tilt mount/pod retracts into the nacelle. However, this pocket isn't quite perfect, and the wires can get caught or nipped during movement, which could be disastrous to servo health and flight control. The wiring movement and containment needs to be improved.

StephenCarlson, 2021-11-24:
Fixed in the new Version 2.1 Nacelle Design, pushed at 81abe56c47fa66ecf6d3cfdf3e897b6ba21a7ef4.

StephenCarlson, 2021-11-24:
Also, linking to the Nacelle redesign issue which solved this: #26 .

Closed 2021-11-24.

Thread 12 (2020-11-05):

Center of Mass: Add Hints/Bumps on wings for correct location

StephenCarlson, 2020-11-05:
Issue title says it all. Most R/C planes have a hint of some kind for where the aircraft should balance. On a plank, this is even more needed.

Lumped into this issue is the option to add custom datum points on the aircraft, and a corresponding jig or holder bracket, such that the aircraft can be weighed on a kitchen scale with one end off-scale, such that precision Center-of-Mass measurements can be made for the vehicle.

StephenCarlson, 2021-04-28:
Not quite solved by ede11e9, but a superior solution is implemented. I've added "jacking points" to the nacelles and tail which allow for a Weight-and-Balance Stand to hold the vehicle while measuring the force from exact datum offsets. Specifically, we want to measure the total weight of the vehicle, and then place the vehicle on the two forward jacking points with the motors in the forward position, and then position the tail jacking point on top of the scale, and then conduct the force contribution of the third (tail) jacking point through the scale. As shown below:

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

Having the total force and tail force, we can calculate the exact center-of-mass location. The equation is:
```math
CoM_LeadingEdge_Offset = (TailJackingPointMass * 220mm + (TotalVehicleMass - TailJackingPointMass) * (-29.3mm)) / TotalVehicleMass
```
Remember to remove (tare) the mass of the tail jacking point stand; we only want the actual tail force contribution.

We want the Center-of-Mass Leading-Edge Offset to be, at the absolute maximum, 30mm. 26mm to 28mm is more stable but the further toward the nose the value drifts, the more nose-up trim required. Going past 30mm is hazardous, as the neutral point exists between 34mm and 36mm. The static margin must be sufficient that the vehicle is pitch-stable.

Again, this does not add "balance bumps" to the wing, and I discourage trying to balance this vehicle by hand due to painful experience when I have casually balanced the aircraft in the field, only to later discover that merely balancing on your fingers is very error-prone.

The STLs for the Weight-and-Balance Stand are included in the STLs folder. Constructing it is straight-forward; it uses the same 1.8mm steel rod pieces as are used for the nacelle hinge pin and servo linkages.

StephenCarlson, 2021-10-16:
Reopening this issue, as there will inevitably be folks out there that don't have a digital scale and will insist on the finger-balance-bump method. The solution I've got feels pretty good from the test prints I've made of the "bullseye" as shown here:
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

StephenCarlson, 2021-11-24:
The new CofG bump design is present in the Solar wing variant, pushed at 81abe56c47fa66ecf6d3cfdf3e897b6ba21a7ef4. Will add to the "Vanilla" wing when I get the chance.

StephenCarlson, 2021-12-02:
The Plain/Vanilla wing has been pushed as of ce00e7db2625b679fa5b0644c8a87afdc569e009 . Therefore, now that all variants of the wing have been published, and all variants have the C-of-G bump, this task is resolved. I need to scrape all the text and images from this issue and put it in the regular README, since this explains much about how the balancing method works for both the jackstand digital scale method, and the finger-balancing C-of-G bumps.

StephenCarlson, 2021-12-23:
Quick note: With the new nacelle design, which looks like this:

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

Please use the following equation, which is the same as above but with 55mm instead of 29.3mm.

```math
CoM_LeadingEdge_Offset = (TailJackingPointMass * 220mm + (TotalVehicleMass - TailJackingPointMass) * (-55mm)) / TotalVehicleMass
```

StephenCarlson, 2021-12-23:
The following table ONLY applies for the new nacelle with the conical cusps located at 55mm forward of the leading edge. The Total Aircraft Weight when placed on the scale alone is shown in the left column. The corresponding right value is what the tail apparent weight should show on the digital scale, with the tail support jack tared to zero such that it is not included:

**28mm Center of Gravity - Required Measurements Table with "_New_" 55mm cusp nacelle design**
| Total Aircraft Weight (g) | Measured Tail Weight (g) |
| ------------------------- | ------------------------ |
| 1000                      | 302                      |
| 1020                      | 308                      |
| 1040                      | 314                      |
| 1060                      | 320                      |
| 1080                      | 326                      |
| 1100                      | 332                      |
| 1120                      | 338                      |
| 1140                      | 344                      |
| 1160                      | 350                      |
| 1180                      | 356                      |
| 1200                      | 362                      |
| 1220                      | 368                      |
| 1240                      | 374                      |
| 1260                      | 380                      |
| 1280                      | 386                      |
| 1300                      | 392                      |
| 1320                      | 398                      |
| 1340                      | 404                      |
| 1360                      | 410                      |
| 1380                      | 417                      |
| 1400                      | 423                      |

Closed 2021-12-02.

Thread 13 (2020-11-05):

Serviceable Servo Arms

StephenCarlson, 2020-11-05:
There is currently no way to remove a servo arm/horn without removing the servo from the wing. A shaft/ramp should be subtracted from the wing such that a screwdriver can reach the servo output shaft.

StephenCarlson, 2021-11-04:
I'm considering renaming this Issue or merging it with a new one: Completely Removable Servo Trays. Spending an hour just to remove a dead servo from the wing, while tediously trying to chisel out hot-melt adhesive, is getting really old. This would add complexity to the wing design, but would allow for any size servo to be placed with a unified tray design.

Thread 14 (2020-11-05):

Redefine Trailing-Edge Planform around Rear Rotor

StephenCarlson, 2020-11-05:
The rear trailing edge, for the section between the vertical fins, is arbitrary and at the mercy of the wing blend, and should be reworked to have a true circular cutout while retaining, as much as possible, a nice crisp trailing edge.

While this does tamper with OML, geometry is not altered too far as to merit v2.0.x, may be folded into 1.1.x.

StephenCarlson, 2021-03-25:
Working on v2.0, fixed this easily. Closed.

StephenCarlson, 2021-04-28:
Released in ede11e9.

Closed 2021-03-25.

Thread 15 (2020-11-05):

Hatch/Lid Improvements

StephenCarlson, 2020-11-05:
The Hatch parting-plane is arbitrarily defined, and should be explicitly defined (The slice is at some transcendental angle, and should be explicitly defined to a nice round integer degree). A collateral wish-list item to this is to explicitly define the lip and hole geometry, much like how kayak spray-skirt cockpits/keyholes are standardized.

The current lip seal isn't very good, and the latch/catch geometry can be improved.

OML isn't changed with this issue, but the compatibility from v1.0.x forward is broken.

StephenCarlson, 2021-04-28:
Much better defined in ede11e9. The parting plane is parallel to the aircraft XY coordinate plane, and is 22.0mm offset.

Also, the Hatch definition is released as a STP/STEP file for modification in other CAD systems. This should allow the community to create variants for FPV cameras and other accessories. This and other released CAD definitions have the file name ending as _RELEASED.stp .

StephenCarlson, 2021-11-24:
I think I've reached perfection in the hatch retention method. Over the previous weekend, "for fun", I designed, prototyped, printed and perfected a latch-lock lever/hook mechanism. It uses the old 1.8x24mm nacelle pins for the hinge, so no need to cut new metal pins. Detents hold the lever in the secured position, but I suppose magnets could also be used in a future design, but I'm adverse to this as it would put strong uncontained magnetic fields in close proximity to the flight controller magnetometer. Pushed at 356c2511adc2a96dd797cd49411159d223af6fd2 . I think it is safe to close this issue and assign to Version 2.1.

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

Closed 2021-11-24.

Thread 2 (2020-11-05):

Support 28mm to 30mm Outside-Diameter motors on front tilt nacelles

StephenCarlson, 2020-11-05:
The current design is for the DYS BE1806, which is ancient and out-of-stock almost everywhere. The tilt mounts should be redesigned for any generic 22xx sized motor. This will incur a slight change to the vehicle OML, requiring the nacelles to become a bit fatter.

StephenCarlson, 2020-11-05:
Nacelles needs much more substantial support as well. Perhaps even so far as adding a bearing/bushing?

StephenCarlson, 2021-04-28:
Solved by ede11e9. Any regular 2207 or 2306 motor should fit, given the absolute maximum outside diameter of the bell is less than 30mm. Several T-Motor options such as the Velox and Pacer 2306 and 2207 series fit this just fine, but as these are not as tall as the original BE1806 motor, spacers are needed to elevate the motor to bring the prop arc away from scraping on the front of the nacelle. The spacers also help in using the screws that come with the motor, which are longer and need about 5mm to 6mm of space, which is aided by 3mm spacers.

Note that this was the more critical issue that was blocking most people from being able to build the MiniHawk-VTOL. I hope the new nacelle pockets will be sufficient for the time being, but another nacelle redesign is in order given some recent issues with servo torque strain due to the current linkage torque load paradigm.

Closed 2021-04-28.

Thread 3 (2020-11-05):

Wire Routing: Switch to Channels instead of Tunnels/Conduits, or add as option

StephenCarlson, 2020-11-05:
Reasons for the switch:
- The current wire tunnels are hazardous for trying to get servo pigtail headers to pass through to the main compartment, and for removal.
- When 3D-Printing, having multiple closed-loops in the cross-section means having to produce a retract move, which can cause layer separation issues when the cross-section transitions from a single closed-loop to a pair of closed-loops, i.e. islanding.
- Most molded EPP R/C planes have to resort to this approach, or otherwise must have complex cut-out panels that are installed after wiring is placed. So a precedent already exists for this, and this will allow for easier maintenance of wires on the vehicle.

While having the conduits is a nice clean solution, this is a practical improvement. It will make the bottom of the wing "dirty", and will have to be covered with tape. A minor puzzle to solve implementing this is the interface from the bottom channels to the main compartment; the channel will have to become a tunnel at some point.

StephenCarlson, 2021-04-28:
Solved by ede11e9. All the servo and avionics wires are accessible on the bottom of the wing. This loses the original wing's smooth bottom surface, and dooms the design to require some kind of tape or covering on the bottom to seal the disruption to the airfoil surface. But this is very well worth it considering that the original required fantastic suffering and tears and fighting to install or remove servo wires.

Motor nacelle wires are also surfaced briefly, but remain submerged in the area of the nacelle as the original was.

Closed 2021-04-28.

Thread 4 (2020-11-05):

Add 5050 SMD LED wells and conduits to the tail

StephenCarlson, 2020-11-05:
The wings already have the 5050 SMD LED wells on the wingtips; a nice place to add more LEDs would be the tail aft of the motor, which is already a bit of a unused piece of structure anyway.

StephenCarlson, 2021-04-28:
Solved by ede11e9. While somewhat occluded by the new tail design, the empennage at least has 5050 SMD LED pockets now. Perhaps one day I'll reposition or add these to the winglets or somewhere else on the tail where they are more visible.

Closed 2021-04-28.

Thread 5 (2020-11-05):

Larger Vertical Fins, Combined Strakes

StephenCarlson, 2020-11-05:
The v1.0.x release has poor directional stability, and the tacked-on stop-gap solution with the strakes and cardboard additions should be folded into a larger set of fins which blend into what is currently the strakes.

StephenCarlson, 2020-11-05:
Also, the fin profile is an arbitrary airfoil shape, needs to be replaced with an actual NACA section.

StephenCarlson, 2021-04-28:
Solved by ede11e9. I didn't end up adding a real airfoil shape, but I did consider the NACA 0008 or NACA 0006. The root and tip are constructed by simple bezier splines: The max thickness for the root is 6% at 27% position. The tip profile has 8% thickness at 30%.

Closed 2021-04-28.

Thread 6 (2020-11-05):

Wells in Wings for VTx, Transcievers, extra electronics

StephenCarlson, 2020-11-05:
The only residence of the wings for the present v1.0.x release are the servos. There is plenty of real estate for electronics in the outboard sections of the wings, at the risk of increasing rotational inertia in the roll axis. Well would likely be hexagon or square cutouts with provisions for a formed hatch to retain the original OML of the wing.

StephenCarlson, 2021-04-28:
Mostly solved by ede11e9. I'm considering the winglets to be the best place for any transceivers, given we want to separate radio components and antennas as far as possible on a platform like this, but I also understand that it increases the roll inertial by doing this. Mounting avionics in the wing is possible, but given that the wings can have solar cells embedded in the top surface, it would be inviting more complexity to establish the precedent that radios can stick out of the wing surface.... I'll probably add avionics pockets to the wings in the future; for now, winglets should do.

StephenCarlson, 2021-12-02:
New winglet in ce00e7db2625b679fa5b0644c8a87afdc569e009 . Mentioning #21 here for the record. The new winglet fully conceals the GPS pocket now, so this means two things: First, the aerodynamics and polish are much better, but Second, building the aircraft is slightly more complicated. The GPS and pitot pressure sensor, which both live in the pocket, will need to be installed into the winglet first, and then the winglet is glued onto the wing. If the winglet is printed in sections, that is one way to avoid this, but it still means some part of the winglet is glued on after the fact. Is it worth it? I think so, as the GPS is now much better protected, the pitot-probe pressure sensor is better shielding from incident light getting into it, and everything looks nicer. The hard part will be the pitot pressure tubing during the install.

Closed 2021-04-28.

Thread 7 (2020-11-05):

Chevron Alignment Surface for Nacelles

StephenCarlson, 2020-11-05:
The present nacelle separation cut is a simple extruded curved surface defining the interface between the wing and nacelle. This can be redefined to a V-shaped interface which will ensure proper alignment of the nacelle when being bonded to the wing. Otherwise at present, there is some slight play when gluing nacelles to the wing interface.

StephenCarlson, 2021-11-24:
I'm just going to keep what I've got; the vertical stabilizers will have the chevron, but I'll hold off of implementing the same feature on the nacelles. Pushed at 81abe56c47fa66ecf6d3cfdf3e897b6ba21a7ef4.

Closed 2021-11-24.

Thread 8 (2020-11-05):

Center of Mass Issues: Lengthen Nose by 22.5mm

StephenCarlson, 2020-11-05:
The v1.0.x flight test vehicle is rather tail-heavy. 60 to 80 grams of ballast were added to the nose, which could be reduced by increasing nose length. This would also make the mounting holes for the battery tray and flight-controller tray be on the same 50mm grid. Doing this however obviously tampers with the vehicle OML, and should merit incrementing to v2.0.x.

StephenCarlson, 2021-04-28:
Solved in ede11e9, and is the primary change to the OML. The nose was stretched much further than the suggested 22.5mm. The new configuration has stanchions all aligned to 50mm pitch spacing (the previous design had an awkward gap of 25mm between sets), with the grid aligned to 30mm behind the front leading edge of the wing. There is an "odd" spare stanchion included for future use, such as reverting from the new positioning of battery and flight controller back to the original configuration.

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

Shown below, the battery is now located ahead of the flight controller. This is necessary to get the vehicle to balance at or before 30mm back from the wing leading edge. This is also beneficial to the flight controller, as coriolis forces are reduced to negligable by being located near the Center of Mass. Lead can still be placed in the nose for fine-tuning the balance.

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
(Note that the PixRacer model seen here is not the PixRacerPro, and that 6 output pins is not sufficient for flying this vehicle. The model is only used as a representation for whatever flight controller is used.)

Closed 2021-04-28.

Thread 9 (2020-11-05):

Explicit Internal Geometry (Infill, Ribs), Partial Skin Generation

StephenCarlson, 2020-11-05:
Currently, Cura, or whatever slicer program is used for 3D Print GCode generation, defines the internal geometry of all structures. This has worked fine, but most modern 3D-printed aircraft have the internal spars, ribs and stringers defined explicitly in the 3D model, and the slicer simply treats everything as walls. An explicit structure would be nice for providing an unambiguous model, and allow for stress analysis and optimization.

Related to explicit internals is finding a way to exclude certain regions of surface skin from printing. The internal walls of the main compartment, for example, are redundant and unnecessary. Large sections of the wing could have 3D-printed skin omitted in favor of film or tape covering.

pbreed, 2023-01-15:
Also some of the larger Resin printers can now print this model, so the defined infil/internal structure STL's would be useful for this as well...

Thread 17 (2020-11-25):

Fix Surface Geometry Flaw on Wingtips/caps

StephenCarlson, 2020-11-25:
Using the Surface Analysis Studying Inspector, I've found some flaws in the design along the wingtips. The Gaussian Curvature visual shows that the blend is flawed with ripples. This needs to be reworked. Image:

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

StephenCarlson, 2021-04-28:
Still exists as of ede11e9.

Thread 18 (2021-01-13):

Create reduced-resolution STLs of moving assembly members for simulation/SITL

StephenCarlson, 2021-01-13:
I've received requests for the MiniHawk-VTOL to have STLs or STEP files available for usage in programs such as RealFlight. I've accomplished this in the past for an early version of the MiniHawk, such as shown in this video using Gazebo: https://www.youtube.com/watch?v=hnc7Bo4m9Y8 .

StephenCarlson, 2021-01-14:
Resolved with 278a0ab

Closed 2021-01-14.

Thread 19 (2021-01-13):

Hardpoints and Belly-Pod Attachment points

StephenCarlson, 2021-01-13:
As if this isn't already complicated enough, this objective is to add hardpoints on the underside of the wings, with supporting wiring conduits. This will provide a way for attachments to be developed and added.

A "Belly-Pod", similar to what the ARA Nighthawk had and what the Cessna 208 Caravan uses, is also a valid target for adding.

StephenCarlson, 2021-12-14:
Adding to this: There have been some requests for landing gear. I would only add that as a possible attachment to the hardpoints mentioned here, rather than modify the belly/fuselage or something else.

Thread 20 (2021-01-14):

Add mount option for pitot tube into wings

nhadrian, 2021-01-14:
Measuring airspeed is really useful (mandatory) if you'd like to tune plane perfectly for auto missions.

StephenCarlson, 2021-04-28:
Solved in ede11e9. The wings have the shaft for the tube defined, assuming 4mm diameter and some allowance for the bend static-port nipple when inserting the assembly. The tube is angled 3 degrees down to correspond to the lower side of the airspeed range. The winglet GPS pocket removal includes a space for the pitot pressure sensor; the pressure sense lines are routed from the pitot probe pocket in the wing to the pressure sensor at the winglet.

Closed 2021-04-28.

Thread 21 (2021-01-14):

Add mount possibility for RF modules and antennas into the wing, near the wing-tip

nhadrian, 2021-01-14:
Placing vTx or telemetry and antenna far from other electronics would improve flight range and video quality.

StephenCarlson, 2021-01-14:
Near duplicate of #6 , but with added detail about antenna placement. Agree that antennas should be at wingtips. Also related: #19

StephenCarlson, 2021-04-28:
Solved by ede11e9, also see #6 , pretty much the same thing.

Closed 2021-04-28.

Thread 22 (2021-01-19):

Branding and Logo Design

StephenCarlson, 2021-01-19:
This project needs a good logo. The following guidelines are suggested:

- It probably isn't a good idea to use the aircraft outline or shadow/form as part of the icon. As the aircraft design shape changes, this will not age well.
- Perhaps a bird outline will do, but something that evokes "VTOL" in the imagery. "Mini" and "Hawk".
- The entire text should be only the following "MiniHawk-VTOL", with the option for VTOL being separate and below and stylized differently from the rest. "MiniHawk-VTOL" is one line, no spaces, and CamelCase capitalization for the 'M' and 'H' in the name.
- The logo should be able to be reproduced using only written instructions, and mildly accessible to anyone with a copy of Inkscape? Anything too complicated or specific to a particular image editing suite will make it difficult to maintain or reproduce in the future.
- Obviously, the logo should be in vector format, and rendered at various sizes.
- The precursor to the MiniHawk was the OrangeHawk, which had a simple text logo (Orange Cursive Font with black outline) as seen in this image here: https://diydrones.com/profiles/blogs/orange-hawk-vtol-update-december-2013 . The Cursive font is lost to my current laptop file collection, I'll have to dig to find the actual font used. It might be best to use this font and simply repeat in the same manner.
- Making a social media square logo for the project necessitates that there be an actual logo design, so simply doing the name in cursive font isn't going to work.....

Here are some excellent references from the UAV world to imitate:
https://px4.io/brand-guidelines/
https://ardupilot.org/dev/docs/trademark.html
https://commons.wikimedia.org/wiki/File:SpaceX-Logo.svg
https://github.com/betaflight/betaflight/blob/master/docs/assets/images/bf_logo.png

StephenCarlson, 2021-01-28:
Possible Fonts for the logo:
https://fontsgeek.com/fonts/Megahertz-In-Regular
https://fontsgeek.com/freestyle-script-font

nermish, 2021-09-04:
while a graphic designer I am not, your ask for a bird with VTOL themes immediately made me think of a Kestrel. They're known for their odd hunting practice of hovering at altitude with remarkable stability, and have a very recognizable silhouette. I threw this together in the last hour or so, feel free to use it if you like it, or if not, maybe it'll spark an idea for someone else later on!

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
[MiniHawkVtol-SVG.zip](https://github.com/StephenCarlson/MiniHawk-VTOL/files/7109307/MiniHawkVtol-SVG.zip)

hope this project isn't dead, looks very promising!

StephenCarlson, 2021-09-04:
@nermish  Thank you so much for the logo, this helps! The project is definitely not dead, just in a very weak stealth mode :) . Per the Hackaday.io post I made in April, I've been wanting to make some grand release with an awesome music video to boot, but being saturated with research all summer, I've been unable to really focus on it that. (Connected to that is updating the readme and parts list.) But the good news; all my summer research has been directly pertaining to this vehicle and some interesting things that you can do with multiple MiniHawks flying at the same time. I've built at least three units of the V2 design as released in April, and have flown each extensively.

My thoughts on the logo:
- I like the Kestrel silhouette, but it will drive me and any other ornithologically-minded people crazy that it isn't a hawk .... if that can be deduced from the silhouette? It's great otherwise! BTW, how did you capture the outline?
- Does the octagon have any driven ratio or driven geometry? As in, what is the curve or tension on the splines that make up the outside perimeter? Reverse-engineering this in Inkscape, it looks like it is made using the polygon tool with Rounded=0.060?
- The hue is a pure share of orange a 24 degrees on the color wheel; mind if that is shifted to 32 or 36 degrees? I guess the text can stay at 26 degrees, or does that look best also shifted to 32/36?
- Imitating the PX4 project, where there are multiple versions of the logo with dark and light versions, below is my modification for a light-version, with sharper corners for the octagon on the outside edge (keeping soft inside corners), and changing the outside color to 32 degrees while retaining 26 degrees for the text:
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

Let me know what you think, lets keep iterating on this, and again, thanks for putting this up!

StephenCarlson, 2021-09-04:
@nermish I also tried a seven-corner outline, if this looks more "cool" and balanced? It has a minor relationship to the planform, which if connecting corners, becomes a seven-corner polygon as well:
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

StephenCarlson, 2021-09-04:
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

nermish, 2021-09-04:
Those revisions look incredible! I agree that the seven pointed outline looks much better, and the rounded internal corners give some good visual depth.

> Regarding bird choice, I'd always heard them called "Sparrow Hawks," and didn't realize they weren't actually hawks. Their outline is decently unique, so if you'd like to try a few others out, to make the silhouette I first  found an image of a hovering one online and loaded it into paint.net (any image editor would work) and used the magic wand selection to select the outline, then filled the whole bird in with a solid color. I took that image to an [online vectorizer](https://www.pngtosvg.com/)  and set the smoothing to a low value so the rough edges disappear. After that i just downloaded the SVG and put that into inkscape!

> I didn't really have any driven dimensions for the polygon, though i probably should have. it was indeed made in inkscape and eyeballed with the polygon tool 😁

>I think the 36 degree orange looks better, it's a bit more vibrant and that's good

>I won't be back at my PC until later today, but I'd also tried a textless version with just the bird that could likely make a good social media logo or graphical signature on documentation, but I couldn't make it look right with the octagon. On the septagonal background, it looks like it'd be much more feasible!

I'm glad I could help with this, feel free to modify that logo until you find something you like, it's yours as far as I'm concerned

StephenCarlson, 2021-09-19:
@nermish I've been working on the logo design some more, but I just realized while looking at my backpack, the grey hawk encircled with an orange/black circle is pretty much the same as the Osprey Backpack company logo. Ugh! Or is that fine?

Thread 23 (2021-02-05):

Wings Designed for Mold-ability, Clamshell Mold Design

StephenCarlson, 2021-02-05:
Considering the severe weight issues that affect the 1.0.x (rev-1) design, and taking into account that issues #1, #3, #6, #7, #12, #13, #17, #19, #20, and #21 all deal with the wings having geometry added or revised, lets contribute to feature bloat by making the wing definitions compatible with wet-layup and/or vacuum prepreg implementations!

Specifically, this target is to have the wings, as defined by the current partitions for 3D printing, have a negative mold available, which will obviously be 3D printed. This negative mold will be a clamshell with a living hinge, such that the molded wing pieces can be removed without destroying the mold, using a seam along the leading edge, or perhaps just below, or along another part of wing geometry. Wing pieces will be attached to the (still) 3D printed body and empennage piece using the regular method (plus spar).

Actual molded material may be fiberglass, carbon-fiber, Kevlar, or a mix. This is somewhat opposite the preferred dream, which is doing an Expanded Polypropylene foam molding process. Related is the idea of making a CNC definition for subtractive milling on a block of EPP. Both these EPP options require expensive equipment; another idea is to use a traditional hot-wire method, but such cannot capture the intricate pockets, curves and cavities that will be present in the wing definition. Perhaps a hot-wire carving "bit" attachment for common 3D printers would do, but that is an entire project unto itself.

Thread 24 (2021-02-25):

Stereo Camera Integration

StephenCarlson, 2021-02-25:
This is related to #21, #19, and #6, but merits a separate issue. For some future version of the design, an array of cameras could be integrated with Field-of-Views optimized to exclude airframe geometry from the image, and to provide multiple baselines for far- and and near-object detection, for forward or isotropic vision. An initial implementation of this could be a simple pair of forward-facing cameras mounted near the tip of each wing.

StephenCarlson, 2021-03-24:
Adjacent to this, a lid was designed for the Khadas VIM3 and Raspberry Pi Model 3B+ Single-Board Computers.

StephenCarlson, 2021-11-24:
The Solar wings now have this feature, with 30x40mm pockets located on the bottom of the wing behind the nacelles, with 240mm center-to-center spacing (same as nacelle spacing). The pockets are large enough to admit a 30x30mm USB board camera, and it is also able to fit the Benewake TFmini Plus with room to spare. Pushed at 81abe56c47fa66ecf6d3cfdf3e897b6ba21a7ef4 .

Closed 2021-11-24.

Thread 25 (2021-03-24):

Removable and Interchangable Wings

StephenCarlson, 2021-03-24:
The support structure for the forward nacelles can be isolated from the rest of the wing, such that the wing can be removed without disrupting the tilt servo and nacelle. The elevon servo and remainder of the wing would be included in the removable element. How the Solar Cells and top wing surface would be unaffected is unknown. This feature would also allow for using different wing variants in an effort to reduce weight and try different implementations; Upper-and-Lower surface 3D printed, Upper-only 3D printed, foam and other variations. The wings contributed the most weight to the vehicle and this would allow for compartmentalizing the issue.

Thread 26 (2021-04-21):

Nacelle Redesign for Zero-Torque Static Condition

StephenCarlson, 2021-04-21:
At least to offer as an option, the nacelles need to be redesigned so that the thrust axis is aligned with and intersects the axis of rotation, such that no torque is conducted to the servo except for overcoming P-factor and gyroscopic dynamics. The primary tradeoff here is that the hinge pin must be split, unless I displace the axis of rotation to be located under the motor, which has issues of being way too cumbersome and allowing the motor to have a long moment-arm which is itself non-zero static torque. Designs like the Eflite Convergence go this route, and I am not a fan of the aesthetics and structure that results. I like having the motor mass being as close to the axis of rotation as possible.

The reason for wanting to implement this is due to the fact that while 2.0 kg*cm of torque is suppose to be more than sufficient, a failure mode has manifested wherein the servo does not strip or burn out completely, but simply loses dynamic output torque capability. This results in transition from hover-to-forward flight absolutely failing, with the aircraft turning into a spinning and tumbling ball of buzzing propellers. I've crashed two prototypes multiple times due to this, and have had very sketchy transitions where it didn't result in a crash. I'm still researching the issue to be sure it is the servo alone that is the cause, but it seems likely.

The downsides of this implementation would be as follows: First, the hinge pin becomes much more complicated as it becomes two separate pins on either side of the motor. Nacelle width is increased. Getting the axis to rotate smoothly is going to be extra effort. Second, servo loading is reduced but servo failure is now masked, and should a servo completely fail, the failure mode is indeterminate. The previous mechanism fail-safes to hover, but this is only useful if the system is commanded to hover on such a failure, otherwise, should the system remain in forward-flight, it would become a ball of buzzing flopping propellers.

StephenCarlson, 2021-11-01:
Repeating an excerpt of some direct messages I've sent to a few folks:
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

StephenCarlson, 2021-11-24:
The new design has been test flown and is working perfectly. Pushed at 81abe56c47fa66ecf6d3cfdf3e897b6ba21a7ef4.

StephenCarlson, 2021-11-24:
Crosslinking to #11; the new nacelle design solves wires getting smashed or fouling the movement.

Closed 2021-11-24.

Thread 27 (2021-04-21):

NACA Ducts for Cooling

StephenCarlson, 2021-04-21:
Pretty much the title. NACA ducts are the common slits/wells seen on various aircraft and race cars which are optimized for spilling air into the interior for cooling. I've tried to keep the body "watertight" as I literally don't want water to get in should the aircraft fly in the rain, but cooling is becoming an issue with ESCs and avionics. I suppose the ducts can be taped over if this is ever needed.

StephenCarlson, 2021-04-28:
Solved in ede11e9. The nose has two variants available in the STLs folder; the NACA Inlet variant is labeled accordingly. I have not added any exhaust vents at this point, as I figure the other holes in the body cavity should be sufficient, not to mention the loose seal that the hatch/lid makes with the lip. If an explicit exhaust hole is needed, it can be drilled or otherwise added by the builder.

Closed 2021-04-28.

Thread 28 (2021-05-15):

Git Restructuring/Branches for Reduced Clone/Fork Size

StephenCarlson, 2021-05-15:
Git is not the optimal version control system for hardware projects, as I understand it. Cloning or forking the repo incurs the burden of downloading all history, which when looking at STL files that are a handful of MB each, and dozens of STL files, each with several version, and it blows up to hundreds of MB. Maybe I'm forgetting that Git does a form of compression? Anyhow, there are probably ways to reduce the burden by branching, or otherwise optimizing the history, if not deleting it somehow. At the project is polished and improved, old versions can only really serve as historical markers, but are dead weight otherwise.

StephenCarlson, 2021-12-14:
Quick update on this: I've made a [development](/StephenCarlson/MiniHawk-VTOL/tree/development) branch and played with updating using this merge mechanism, and it works. Also, the current repo size including the `.git` folder is over 300MB, which is annoying. The fears I had as articulated in May are becoming real; that despite my efforts to minimize repo inflation through carefully commits and management, the baggage and burden of file history is starting to snowball. How do I fix this?

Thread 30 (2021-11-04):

Nacelle Redesign-Redesign: Fat-Footprint Reduction and Bearing Pocket Swap

StephenCarlson, 2021-11-04:
On the verge of finishing #26 , the new design is very fat, almost 40mm wide when viewed from above, which is an increase in the blown surface area and cross-section. I've wasted a bunch of time trying to reduce that footprint to be close to what the v2.0 nacelle was, but too much is getting broken in the process and this can wait until v2.2 or future.

Related to this, the ball-bearing pockets should be shifted to the motor tilt mount, with the retaining shaft secured and bonded at the nacelle side. The current design has the bearing pockets in the nacelle arm/fork, and the motor tilt mount has the retaining shaft bonded. This was to avoid interfering with the motor well, but on review, the motor tilt mount has enough room to support a bearing pocket without intersecting with other geometry.

StephenCarlson, 2021-11-19:
Design also needs to address any contact with the ground; this new design drops the tilt linkages lower and they can contact the ground rest plane before the wingtips do.

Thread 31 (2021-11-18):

Offer Reduced-Height Sections of the Wings and Nose

StephenCarlson, 2021-11-18:
The complaints have piled up, and while I've dragged my feet on this, (since, in my mind, the complaint is somewhat lazy and I can only appease the issue with a totally arbitrary threshold)..... I shall finally relent. The Wings and Nose need to be offered in shorter sections. I do hope that this is the first and last occurrence of the issue: If parts are too big going forward, please, I beg of you all, just use the Part Intersection Modifier feature of your slicer software to section the print volume manually. :)

The Creality Ender 3 is selected as the template/example for the volume/height of sectioned parts. That is, the nose and wings will be sectioned so that each piece is less than 250mm tall. The Ender 3 Build Plate is 220x220mm, so the wing pieces may need to be slightly rotated to fit on the plate.

StephenCarlson, 2021-11-18:
Partially solved with 9593709, the solar wings are NACA-Duct nose are sectioned at _A and _B parts.

StephenCarlson, 2021-12-02:
Fully finished at ce00e7db2625b679fa5b0644c8a87afdc569e009. The wings have two variations as usual: The Plain/Vanilla Wing with no solar cells or extra pockets, and the Solar wing with solar cell plumbing and extra pockets for robotics cameras and sensors. Both version have _A and _B inboard / outboard sections explicitly defined for printing on shorter printers. The nose ... oh, I guess I have not sectioned the plain nose ... I forgot the plain nose existed. Ahem, the nose is also sectioned for shorter printers; lets pretend that there isn't yet another nose version out there!

Closed 2021-12-02.

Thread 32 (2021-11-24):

Offer the Avionics Tray and Battery Tray Variants as DXF, SVG

StephenCarlson, 2021-11-24:
For those that want to laser-cut or mill the trays, this makes sense. It is possible that the outlines can be pulled from the STLs, but this makes life easier.

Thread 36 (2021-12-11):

README: Add a Tree Diagram of the Assembly Decomposition

StephenCarlson, 2021-12-11:
The assembly is super confusing right now. All these _A and _B parts, why is there only a Left side of anything? Which parts need to be printed? These are all things that are either barely documented in the #airframe-parts- section, or are implicit in the name of the STLs. Here is a quick synopsis:
- For parts such as the Wings and Vertical Stabilizers and Winglets, only the left STL is included, since these are easily mirrored to the Right-side version in whatever slicer these are pulled into. There is no point to including a Right-side of each of these STLs since it increases the number of parts in the repository, and increases the number of steps for each release. But.... you know what, at this point, whatever, data is cheap, right? Fine, I'll add a Right of every STL, [grumbling intensifies as I add this to the ToDo list].
- For pieces that are non-chiral (cannot be mirrored self-similarly), these have a _A and _B suffix in the name. The Nacelles are definitely non-chiral, as one side (the outer or closest to wingtip) is the side that has the geometry for the servo linkage, and the inside (nearest the fuselage) is "normal". This convention is also used where pieces that are available as one piece are split into two pieces for convenience for those with smaller 3D printers. The Nose and Wings have this, where if you cannot print the whole thing, there are the _A and _B options.
- A graphical decomposition needs to be made using my CAD system's assembly artwork annotation functions. I need to edit the assembly where all the parts are animated/exploded to show relationships. More work....
- The Tree Diagram should use ASCII characters and look nice in both the raw Markdown text, and as rendered on GitHub.

Here is an example, or root node, of the Tree Diagram:

MiniHawk-VTOL Version 2.1 Aircraft
| -- Fuselage/Body
|    |-- Empennage
|    |-- Nose
|-- Left Wing
|    |-- Left Fin
|    |    |-- MH7_FinLeft_Lower.stl
|    |    |-- MH7_FinLeft_Upper.stl
|-- Right Wing
|    |-- Right Fin
|    |    |-- MH7_FinLeft_Lower.stl (Mirrored)
|    |    |-- MH7_FinLeft_Upper.stl (Mirrored)

LilBub, 2021-12-11:
Hi Steve,  I think you'll make the build easier for others who aren't engineering / student types if you include everything needed once.  No mirrored parts since, for some not savvy with 3D slicers, could get it wrong.  So, as I do with my technical documentation (research 3D printing for military projects), make the outline has clear and concise as possible.  Also, know you audience may be less smart as you =)

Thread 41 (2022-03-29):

Paper available?

github-throwaway, 2022-03-29:
Hi Stephen,

I'm currently writing my master's thesis about UAS in search and rescue. I think your project is fascinating. Would you be able to share your paper **[The MiniHawk-VTOL: Design, Modeling, and Experiments of a Rapidly-prototyped Tiltrotor UAV](https://ieeexplore.ieee.org/abstract/document/9476731)**?

StephenCarlson, 2022-03-29:
Yep! Here is where I've previously posted a copy of the PDF: https://github.com/StephenCarlson/MiniHawk-VTOL/discussions/40#discussioncomment-2224433

Closed 2022-03-29.

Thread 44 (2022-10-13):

Convert rear to pusher prop in forward motion?

cchance27, 2022-10-13:
Just wondering why not transition the rear prop into a pusher prop during forward flight? Seems its almost setup to work if you used the same pod style from the form in stead of the arm from the back

StephenCarlson, 2022-11-26:
Sorry for the delay. My stance is... no, it is not appropriate to have all the motors participate in all modes of flight. Each motor/set is specialized/optimized for their respective role. It is important to realize that each motor/rotor has a Thrust-Available curve (see _Introduction to Flight_ by John D. Anderson Jr., Chapter 6.4), with zero-velocity static (hover) thrust on one edge intersection, and the pitch-speed (near-zero thrust force) occurring on the orthogonal edge intersection. Adding forward-flight rotors will increase total thrust available, but the pitch speed for each rotor remains an individual attribute, and if the rear rotor is optimized for hover, its pitch speed will be rather low, to that point that having it try to participate in forward flight is actually quite wasteful and even damaging to efficiency. The MiniHawk already, with just two 5-inch props on the front, is capable of climbing vertically. Really, it needs smaller motors on the front that are tuned for 20m/s, but the prop discs must be large enough to contribute correctly during hover, so we are a bit stuck with 5-inch props and inefficient forward cruise.

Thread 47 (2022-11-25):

Enhancement camera embedded in  nosecone

davidabevan, 2022-11-25:
Thanks for great work so far.
Am attempting this as winter project. My 2nd ardupilot vtol. I am wondering if a new nosecone can incorporate the fpv camera in the front or such like. Yes the possibility of camera damage is there but lots of fpv planes do use this approach. Hopefully you can think on this maybe adapt your design later. Thanks for sharing project.

StephenCarlson, 2022-11-26:
I like leaving the nose tip empty for use as a ballast location. (I use between 10g and 40g of lead weight in the nose tip for my MiniHawks.) The FPV Hatch/Lid STL can support a 15mm cube camera and VTX just fine while keeping it out of the dirt and damage. But, yeah, I agree that the placement is somewhat annoying if you want to see the bottom-arch of the video feed that is obscured by the nose for that position.

davidabevan, 2022-11-26:
Thanks for getting back to me.. Ok no probs.
Ive also read your comments on the "Jumper Fiasco" I totally agree with you and think they are completely in the wrong. It also appears they made a Lemon due to substandard electronics no dshot esc and FC reboots. NO Compass  WHAT>>>>Just think what COULD have happened with some collaboration between yourself and the ardupilot community.
My Thanks and support Dave B

davidabevan, 2022-12-07:
Thanks for Reply Sorry I forgot to close...

Closed 2022-12-07.

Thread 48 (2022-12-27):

CAD files

madhunm, 2022-12-27:
Stephen,

Do you think it would be possible to release the CAD files (STEP format) for the latest revision of MiniHawk?

Thanks!

StephenCarlson, 2023-01-19:
@madhunm That.... is a very relevant question, and one I'm grappling with. I released the Hatch here on GitHub in STEP format, in the hopes that it would allow others to make custom hatch mods, but I held off from giving all the STLs the STEP treatment since it would make reverse-engineering the design for mass production a breeze, and I figured that I would re-evaluate that decision if the hatch STEP mods idea got popular. Well, the drama of the past few months with Jumper reusing the MiniHawk for an unsanctioned and unattributed commercial implementation has shown that releasing the majority of the aircraft in STL format only ( which is relatively low-res compared to STEP) didn't stop them from running with it anyway. (Also note that I released the Nacelle design as a STEP assembly to the Facebook VTOL Hangout Group, I had hoped that the more tight-knit community there might be a safer place to post that, but it may well have also been scraped by Jumper.)

A few ideas for what I can do:
1. Keep the pattern that currently exists: Only STLs except a few select STEP files.
2. Provide the STEP version to individuals on a case-by-case basis
3. Release everything as STEP.

I'm leaning toward the second option. What would you like to do with the STEP version?

-Steve

jhiggason, 2023-01-27:
Do you have a post talking about the Jumper drama?  It does look like they completely ripped off your design...I kind of liked some of the jumper products but will stop buying them if they are straight up just ripping off others work.  (I'm trying to find a good, low cost radio to reccomend to my "customers" and will definately not be using jumper if this is their typical business practice)

StephenCarlson, 2023-01-27:
Yep, it is discussed here, just one tab over in "Discussions". https://github.com/StephenCarlson/MiniHawk-VTOL/discussions/46

EreminAleksey, 2023-11-06:
Hi Stephen.
Could you please provide the minihawk step files. I want create and make 3d prinded molds for polyurethane foam. I don`t want to buy xiake800 body, because jumper stole your project.

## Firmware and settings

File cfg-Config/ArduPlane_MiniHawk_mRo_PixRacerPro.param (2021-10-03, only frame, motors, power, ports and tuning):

BATT_AMP_OFFSET,0
BATT_AMP_PERVLT,37.03995
BATT_ARM_MAH,0
BATT_ARM_VOLT,0
BATT_BUS,0
BATT_CAPACITY,1300
BATT_CRT_MAH,0
BATT_CRT_VOLT,0
BATT_CURR_PIN,15
BATT_FS_CRT_ACT,0
BATT_FS_LOW_ACT,0
BATT_FS_VOLTSRC,0
BATT_LOW_MAH,0
BATT_LOW_TIMER,10
BATT_LOW_VOLT,0
BATT_MONITOR,4
BATT_OPTIONS,0
BATT_SERIAL_NUM,-1
BATT_VOLT_MULT,15.3
BATT_VOLT_PIN,14
BATT_WATT_MAX,0
BATT2_MONITOR,0
BATT3_MONITOR,0
BATT4_MONITOR,0
BATT5_MONITOR,0
BATT6_MONITOR,0
BATT7_MONITOR,0
BATT8_MONITOR,0
BATT9_MONITOR,0
FLTMODE_CH,5
FLTMODE1,5
FLTMODE2,19
FLTMODE3,17
FLTMODE4,17
FLTMODE5,17
FLTMODE6,10
INS_GYRO_FILTER,20
INS_HNTCH_ENABLE,0
Q_A_ACCEL_P_MAX,110000
Q_A_ACCEL_R_MAX,110000
Q_A_ACCEL_Y_MAX,27000
Q_A_ANG_LIM_TC,1
Q_A_ANG_PIT_P,4.5
Q_A_ANG_RLL_P,6
Q_A_ANG_YAW_P,5
Q_A_ANGLE_BOOST,1
Q_A_INPUT_TC,0.2
Q_A_RAT_PIT_D,0.0005
Q_A_RAT_PIT_FF,0
Q_A_RAT_PIT_FLTD,15
Q_A_RAT_PIT_FLTE,0
Q_A_RAT_PIT_FLTT,20
Q_A_RAT_PIT_I,0.15
Q_A_RAT_PIT_IMAX,0.5
Q_A_RAT_PIT_P,0.15
Q_A_RAT_PIT_SMAX,0
Q_A_RAT_RLL_D,0.003
Q_A_RAT_RLL_FF,0
Q_A_RAT_RLL_FLTD,15
Q_A_RAT_RLL_FLTE,0
Q_A_RAT_RLL_FLTT,20
Q_A_RAT_RLL_I,0.25
Q_A_RAT_RLL_IMAX,0.5
Q_A_RAT_RLL_P,0.45
Q_A_RAT_RLL_SMAX,0
Q_A_RAT_YAW_D,0.02
Q_A_RAT_YAW_FF,0.1
Q_A_RAT_YAW_FLTD,0
Q_A_RAT_YAW_FLTE,10
Q_A_RAT_YAW_FLTT,20
Q_A_RAT_YAW_I,0.1
Q_A_RAT_YAW_IMAX,0.5
Q_A_RAT_YAW_P,0.6
Q_A_RAT_YAW_SMAX,0
Q_A_RATE_FF_ENAB,1
Q_A_RATE_P_MAX,0
Q_A_RATE_R_MAX,0
Q_A_RATE_Y_MAX,0
Q_A_SLEW_YAW,2000
Q_A_THR_MIX_MAN,0.5
Q_A_THR_MIX_MAX,0.5
Q_A_THR_MIX_MIN,0.1
Q_M_BAT_CURR_MAX,0
Q_M_BAT_CURR_TC,5
Q_M_BAT_IDX,0
Q_M_BAT_VOLT_MAX,0
Q_M_BAT_VOLT_MIN,0
Q_M_BOOST_SCALE,0
Q_M_HOVER_LEARN,2
Q_M_PWM_MAX,2000
Q_M_PWM_MIN,1000
Q_M_PWM_TYPE,4
Q_M_SAFE_DISARM,0
Q_M_SAFE_TIME,1
Q_M_SLEW_DN_TIME,0
Q_M_SLEW_UP_TIME,0
Q_M_SPIN_ARM,0.05
Q_M_SPIN_MAX,1
Q_M_SPIN_MIN,0.1
Q_M_SPOOL_TIME,0.5
Q_M_THST_EXPO,0.25
Q_M_THST_HOVER,0.3
Q_M_YAW_HEADROOM,50
Q_M_YAW_SV_ANGLE,12
SERIAL0_BAUD,115
SERIAL0_PROTOCOL,2
SERIAL1_BAUD,57
SERIAL1_OPTIONS,0
SERIAL1_PROTOCOL,2
SERIAL2_BAUD,57
SERIAL2_OPTIONS,0
SERIAL2_PROTOCOL,2
SERIAL3_BAUD,38
SERIAL3_OPTIONS,0
SERIAL3_PROTOCOL,5
SERIAL4_BAUD,38
SERIAL4_OPTIONS,0
SERIAL4_PROTOCOL,-1
SERIAL5_BAUD,57
SERIAL5_OPTIONS,0
SERIAL5_PROTOCOL,-1
SERIAL6_BAUD,57
SERIAL6_OPTIONS,0
SERIAL6_PROTOCOL,-1
SERIAL7_BAUD,57
SERIAL7_OPTIONS,0
SERIAL7_PROTOCOL,-1
SERVO1_FUNCTION,33
SERVO1_MAX,2000
SERVO1_MIN,1000
SERVO1_REVERSED,0
SERVO1_TRIM,1500
SERVO2_FUNCTION,34
SERVO2_MAX,2000
SERVO2_MIN,1000
SERVO2_REVERSED,0
SERVO2_TRIM,1500
SERVO3_FUNCTION,0
SERVO3_MAX,1900
SERVO3_MIN,1100
SERVO3_REVERSED,0
SERVO3_TRIM,1100
SERVO4_FUNCTION,36
SERVO4_MAX,2000
SERVO4_MIN,1000
SERVO4_REVERSED,0
SERVO4_TRIM,1500
SERVO5_FUNCTION,75
SERVO5_MAX,1800
SERVO5_MIN,1200
SERVO5_REVERSED,0
SERVO5_TRIM,1500
SERVO6_FUNCTION,76
SERVO6_MAX,1800
SERVO6_MIN,1200
SERVO6_REVERSED,1
SERVO6_TRIM,1500
SERVO7_FUNCTION,77
SERVO7_MAX,1900
SERVO7_MIN,1100
SERVO7_REVERSED,1
SERVO7_TRIM,1520
SERVO8_FUNCTION,78
SERVO8_MAX,1900
SERVO8_MIN,1100
SERVO8_REVERSED,0
SERVO8_TRIM,1480
SERVO9_FUNCTION,0
SERVO9_MAX,1900
SERVO9_MIN,1100
SERVO9_REVERSED,0
SERVO9_TRIM,1500

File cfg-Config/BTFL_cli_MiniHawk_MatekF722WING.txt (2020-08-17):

# diff all

# version
# Betaflight / MATEKF722SE (MF7S) 4.3.0 Jul 27 2020 / 16:52:58 (norevision) MSP API: 1.44

# start the command batch
batch start

# reset configuration to default settings
defaults nosave

board_name MATEKF722SE
manufacturer_id MTKS
mcu_id 001700353238510e36353235
signature 

# name: MiniHawk

# resources
resource MOTOR 1 B06
resource MOTOR 2 B07
resource MOTOR 3 A15
resource MOTOR 4 B03
resource MOTOR 5 NONE
resource MOTOR 6 NONE
resource MOTOR 7 NONE
resource MOTOR 8 NONE
resource SERVO 1 B04
resource SERVO 2 B05
resource SERVO 3 B00
resource SERVO 4 B01

# feature
# Uncomment both lines below for PPM Receiver, or as required
#feature -RX_SERIAL
#feature RX_PPM
feature MOTOR_STOP

# serial
serial 3 2048 115200 57600 0 115200

# mixer
mixer CUSTOMAIRPLANE
mmix 0  1.000  1.000 -0.667  0.000
mmix 1  1.000 -1.000 -0.667  0.000
mmix 2  1.000  0.000  1.333  0.000

# servo mixer
smix 0 4 2 -10 0 0 100 2
smix 1 5 2 -10 0 0 100 2
smix 2 4 2 -50 0 0 100 3
smix 3 5 2 -50 0 0 100 3
smix 4 4 8 100 1 0 83 0
smix 5 5 8 -100 1 17 100 0
smix 6 2 4 50 0 0 100 0
smix 7 3 4 50 0 0 100 0
smix 8 2 5 50 0 0 100 0
smix 9 3 5 -50 0 0 100 0
smix 10 2 0 20 0 0 100 1
smix 11 3 0 20 0 0 100 1
smix 12 2 1 20 0 0 100 1
smix 13 3 1 -20 0 0 100 1
smix 14 2 11 50 0 0 100 0
smix 15 3 11 -50 0 0 100 0

# vmix
vmix 0 4  1.000  0.000  0.390  0.720  0.940  1.000
vmix 1 4  1.000  0.000  0.390  0.720  0.940  1.000
vmix 2 4  0.000  0.000  0.390  0.720  0.940  1.000
vmix 3 0  0.000  0.000  0.000  0.000  0.000  0.000
vmix 4 0  0.000  0.000  0.000  0.000  0.000  0.000
vmix 5 0  0.000  0.000  0.000  0.000  0.000  0.000
vmix 6 0  0.000  0.000  0.000  0.000  0.000  0.000
vmix 7 0  0.000  0.000  0.000  0.000  0.000  0.000

# beacon
beacon RX_LOST
beacon RX_SET

# aux
aux 0 1 1 1400 2100 0 0
aux 1 27 1 1800 2100 0 0
aux 2 13 1 1800 2100 0 0
aux 3 23 2 1600 2100 0 0
aux 4 24 0 1325 1675 0 0
aux 5 25 0 1675 2100 0 0
aux 6 28 2 1600 2100 0 0

# vtxtable
# Configured for the AKK Infinite DVR VTx
vtxtable bands 5
vtxtable channels 8
vtxtable band 1 BOSCAM_A A FACTORY 5865 5845 5825 5805 5785 5765 5745 5725
vtxtable band 2 BOSCAM_B B FACTORY 5733 5752 5771 5790 5809 5828 5847 5866
vtxtable band 3 BOSCAM_E E FACTORY 5705 5685 5665    0 5885 5905    0    0
vtxtable band 4 FATSHARK F FACTORY 5740 5760 5780 5800 5820 5840 5860 5880
vtxtable band 5 RACEBAND R FACTORY 5658 5695 5732 5769 5806 5843 5880 5917
vtxtable powerlevels 4
vtxtable powervalues 0 1 2 3
vtxtable powerlabels 25 200 600 1K

# rxfail
rxfail 4 s 2000
rxfail 5 h
rxfail 6 s 2000

# master
# Accelerometer calibration provided for reference below, do not reuse.
# set acc_calibration = 271,79,291,1
set mag_hardware = NONE
set min_throttle = 1000
set dshot_idle_value = 0
set motor_pwm_protocol = DSHOT600
set motor_pwm_rate = 16000
set failsafe_off_delay = 100
set failsafe_throttle = 1300
set failsafe_procedure = AUTO-LAND
set bat_capacity = 1200
set ibata_scale = 250
set beeper_dshot_beacon_tone = 3
set osd_warn_batt_not_full = OFF
set osd_warn_over_cap = ON
set osd_cap_alarm = 1100
set osd_alt_alarm = 999
set osd_tim1 = 0
set osd_tim2 = 1
set osd_vbat_pos = 2369
set osd_tim_1_pos = 407
set osd_tim_2_pos = 2455
set osd_flymode_pos = 2177
set osd_g_force_pos = 2265
set osd_throttle_pos = 2393
set osd_crosshairs_pos = 2254
set osd_ah_pos = 2127
set osd_current_pos = 2401
set osd_mah_drawn_pos = 2433
set osd_motor_diag_pos = 2425
set osd_craft_name_pos = 2443
set osd_altitude_pos = 2102
set osd_warnings_pos = 14442
set osd_nvario_pos = 2134
set osd_core_temp_pos = 2241
set osd_log_status_pos = 2273
set osd_stat_max_spd = OFF
set osd_stat_min_rssi = OFF
set osd_stat_max_g_force = ON
set osd_stat_total_time = ON
set debug_mode = GYRO_SCALED
set enable_stick_arming = ON
set vtx_band = 4
set vtx_channel = 1
set vtx_power = 1
set vtx_freq = 5740
set name = MiniHawk

profile 0

# profile 0
set pid_at_min_throttle = OFF
set p_pitch = 40
set i_pitch = 30
set d_pitch = 20
set f_pitch = 0
set p_roll = 120
set i_roll = 60
set d_roll = 10
set f_roll = 0
set p_yaw = 60
set i_yaw = 5
set f_yaw = 0
set angle_level_strength = 30
set horizon_level_strength = 30
set d_min_roll = 0
set d_min_pitch = 0

profile 1

# profile 1
set pid_at_min_throttle = OFF
set p_pitch = 40
set i_pitch = 30
set d_pitch = 20
set f_pitch = 0
set p_roll = 120
set i_roll = 60
set d_roll = 10
set f_roll = 0
set p_yaw = 60
set i_yaw = 40
set f_yaw = 0
set angle_level_strength = 30
set horizon_level_strength = 30
set d_min_roll = 0
set d_min_pitch = 0

profile 2

# profile 2
set pid_at_min_throttle = OFF
set p_pitch = 40
set i_pitch = 30
set d_pitch = 20
set f_pitch = 0
set p_roll = 120
set i_roll = 60
set d_roll = 10
set f_roll = 0
set p_yaw = 80
set i_yaw = 10
set d_yaw = 20
set f_yaw = 0
set angle_level_strength = 30
set horizon_level_strength = 30
set d_min_roll = 0
set d_min_pitch = 0

# restore original profile selection
profile 1

rateprofile 0

rateprofile 1

rateprofile 2

rateprofile 3

rateprofile 4

rateprofile 5

# restore original rateprofile selection
rateprofile 0

# save configuration
save
# 

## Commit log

2020-06-15 Added fuselage and lid 3MF artwork.
    [MH5_EmpennageSet.3mf, MH5_LidPair.3mf, MH5_Nose.3mf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]
2020-07-10 Added the rest of the 3MF airframe files, complete set.
    [MH5_ControlHornSet.3mf, MH5_FinSingle.3mf, MH5_NacelleSet.3mf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]
2020-07-13 Added STL File references
2020-07-13 Added STLs, moved 3MF, new folders
    [MH5_BatteryTray.stl, MH5_ControlHorn.stl, MH5_ControlHornSet.3mf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]
2020-07-13 Added CFD STL files
    [MH5_CFD_0deg.stl, MH5_CFD_clean-BREP.stl, MH5_CFD_clean.stl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]
2020-08-17 Added Strake and FPV-Lid variant, renaming
    [BTFL_cli_MiniHawk_MatekF722WING.txt, MH5_Lid-FPV.stl, MH5_RearStrake.stl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]
2020-09-24 Isometric photo of assembly
2021-01-14 Added STLs of geometry-reduced assembly, for use in 3D simulations, etc
    [MH5_SimReduced_Airframe_BREP.stl, MH5_SimReduced_Airframe_LOD-2.stl, MH5_SimReduced_ElevonLeft_BREP.stl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]
2021-02-18 Added ArduPlane .param files for PixRacerPro and RealFlight 9.5
    [ArduPlane_MiniHawk_RealFlight9point5.param, ArduPlane_MiniHawk_mRo_PixRacerPro.param]
2021-04-28 Version 2 of the MiniHawk-VTOL: STLs, Profile Picture
    [ArduPlane_MiniHawk_mRo_PixRacerPro.param, MH7_BatteryTray.stl, MH7_ControllerTray.stl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]
2021-04-28 Winglet fix
    [MH7_WingletLeft-GPS.stl]
2021-06-08 Updated config files for ArduPilot SITL, mRoPixRacerPro
    [ArduPlane_MiniHawk_RealFlight9point5.param, ArduPlane_MiniHawk_mRo_PixRacerPro.param]
2021-09-24 Deleted old MH5 STLs, improved TiltMount, Empennage
    [MH5_BatteryTray.stl, MH5_ControllerTray.stl, MH5_Empennage.stl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]
2021-09-24 Motor direction comment.
2021-09-24 Servo conduits commend.
2021-10-03 3MF files updated to Version 2
    [MH5_ControlHornSet.3mf, MH5_EmpennageSet.3mf, MH5_FinSingle.3mf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]
2021-10-03 Updated default ArduPlane parameters
    [ArduPlane_MiniHawk_mRo_PixRacerPro.param]
2021-10-13 Added NACA-Vent Hatch/Lid
    [MH7_Hatch-Vented.stl]
2021-10-25 Added -Full Tail variant
    [MH7_Empennage-Full.stl]
2021-10-26 Crayon-quality edit to Figure 16, CG is 26-28mm!
2021-11-01 Rear Prop Suggestion
2021-11-12 Added Community Builds thread link
2021-11-18 New Nacelle Design, Solar Wing, Fins added, v2p1
    [MH7_FinLeft_Lower.stl, MH7_FinLeft_Upper.stl, MH7_Nacelle_A-Bearing.stl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]
2021-11-18 Sectioned Wings and Nose, Empennage updated
    [MH7_Empennage.stl, MH7_Nose_A-NacaDucts.stl, MH7_Nose_B.stl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]
2021-11-22 New v2p1 Latch-Locking Vented Hatch
    [MH7_Hatch-Vented.stl, MH7_Hatch-Vented_a.stl, MH7_Hatch-Vented_b.stl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]
2021-12-02 Version 2.1 Plain Wing w/ sections, FPV Lid, GPS Winglet
    [MH7_Hatch-FPV-16mm_a.stl, MH7_Hatch-FPV-16mm_b.stl, MH7_WingLeft.stl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]
2021-12-14 Part 1 of 3MF Renaming/Updates
    [MH7_Fin_Set.3mf, MH7_Hatch-FPV_Set.3mf, MH7_Hatch-Vented2_Set.3mf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]
2021-12-14 Part 2: Renamed files
    [MH7_Hatch-Vented_Set.3mf, MH7_Nacelle-Bearing_Set.3mf, MH7_TiltMount-NoBearing_Set.3mf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]
2021-12-14 Part 3: Added remaining files
    [MH7_Hatch_LockingLatch.3mf, MH7_Nacelle-NoBearing_Set.3mf, MH7_WingLeft-Solar.3mf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]
2021-12-14 Renamed ControllerTray to AvionicsTray
    [MH7_AvionicsTray.3mf, MH7_AvionicsTray2.3mf]
2021-12-14 Fixed stl file ending
    [MH7_AvionicsTray.stl, MH7_AvionicsTray2.stl]
